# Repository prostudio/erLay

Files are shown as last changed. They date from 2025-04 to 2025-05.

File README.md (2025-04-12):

erLay is a ultra-portable CoreXY 3D printer made by [Evan Yu](https://evanyu.dev) and [Aaron Huang](https://runthebot.me)

This printer is built to print small parts needed fast at robotics competitions where our main limitations are space and time. This printer will mainly print spacers, shaft collars, pullies, etc.

## [BOM](https://docs.google.com/spreadsheets/d/1s7m9KlAu-EawWQ5k7trbtZSsV5alHb0_lQaYVRcTUCk/view) | [CAD](https://cad.onshape.com/documents/c8077fee67b983eb99774ac1/w/a53d436f84abc79ea5797123/e/d46022eb7d51b7e61800c962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) | [Journal](https://github.com/Badbird5907/erLay/blob/master/journal.md)

# Goals (we didn't manage to hit all of these within budget)
- Ultra-portable (for robotics competitions!!)
- Pico MMU (Optional) (Not in budget 😭)
- Zero Click ABL (Optional)
- Built-in carrying case (The printer will collapse into something like a pelican case) (Gave up on this one. see journal)
- Can be powered by a (multiple) power banks (Gave up on this one)
- NO STANDARD EXTRUSION (I think they look ewww and too normal)

# Features (Items in the final build)
- Locally sourced frame (Proudly Canadian)
- Easy to disassemble (8 Bolts)
- Core XY
- Klipper
- NeoPixel LEDs

3D Model

# Interesting note on design!
As you will notice, most of the frame is built out of linear rods. I was inspired by hex shafts in FRC and how we tap them and use a bolt to clamp both sides. I decided to do this for infill to maximize rigidity and minimize construction/deconstruction time.

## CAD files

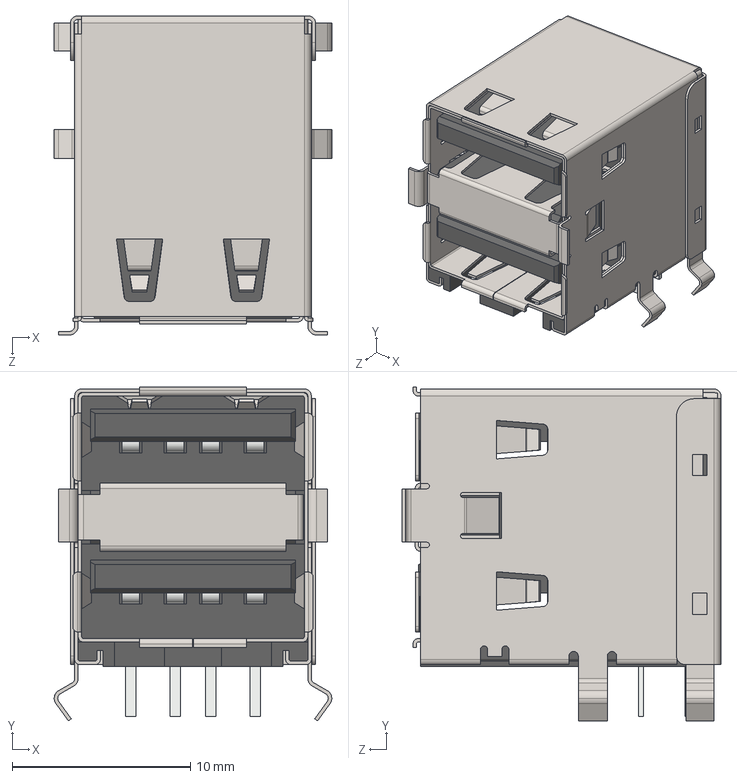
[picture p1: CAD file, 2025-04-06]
IOBoard/Components/usb double.step
15.6 x 18.7 x 17.9 mm

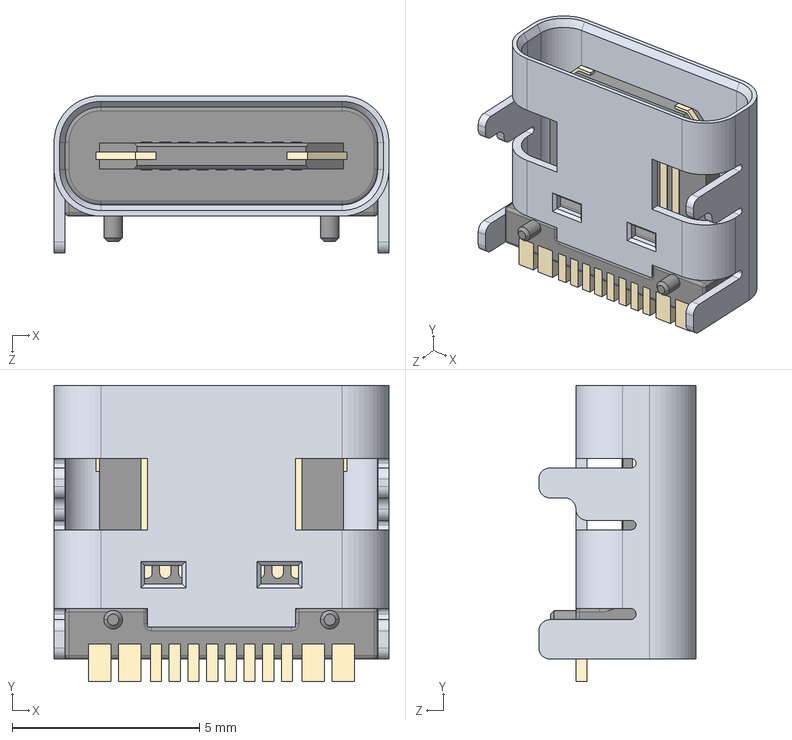
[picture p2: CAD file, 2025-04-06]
IOBoard/Components/usbc.step
8.94 x 7.90 x 4.20 mm

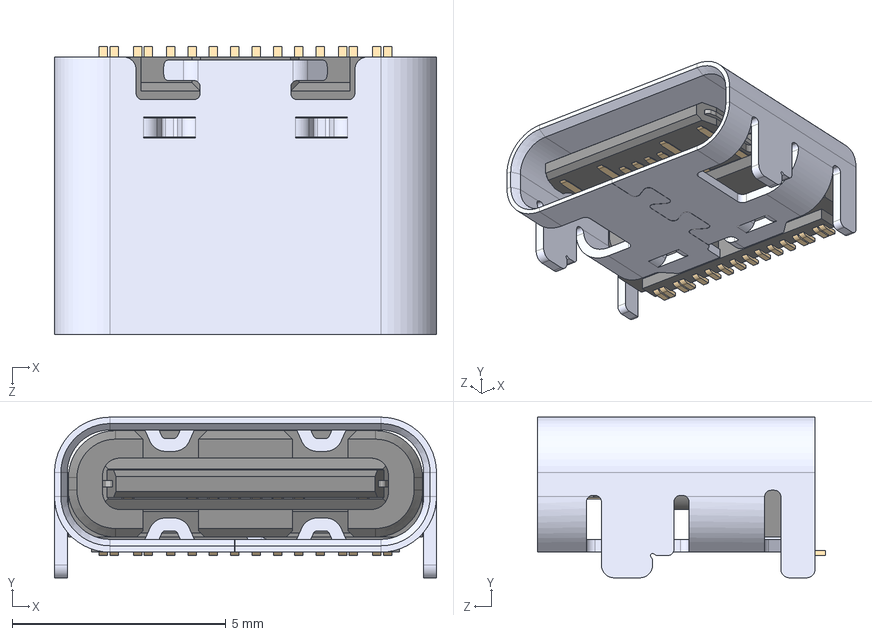
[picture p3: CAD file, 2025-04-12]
IOBoard/Components/2171790001.step
8.94 x 3.76 x 6.75 mm

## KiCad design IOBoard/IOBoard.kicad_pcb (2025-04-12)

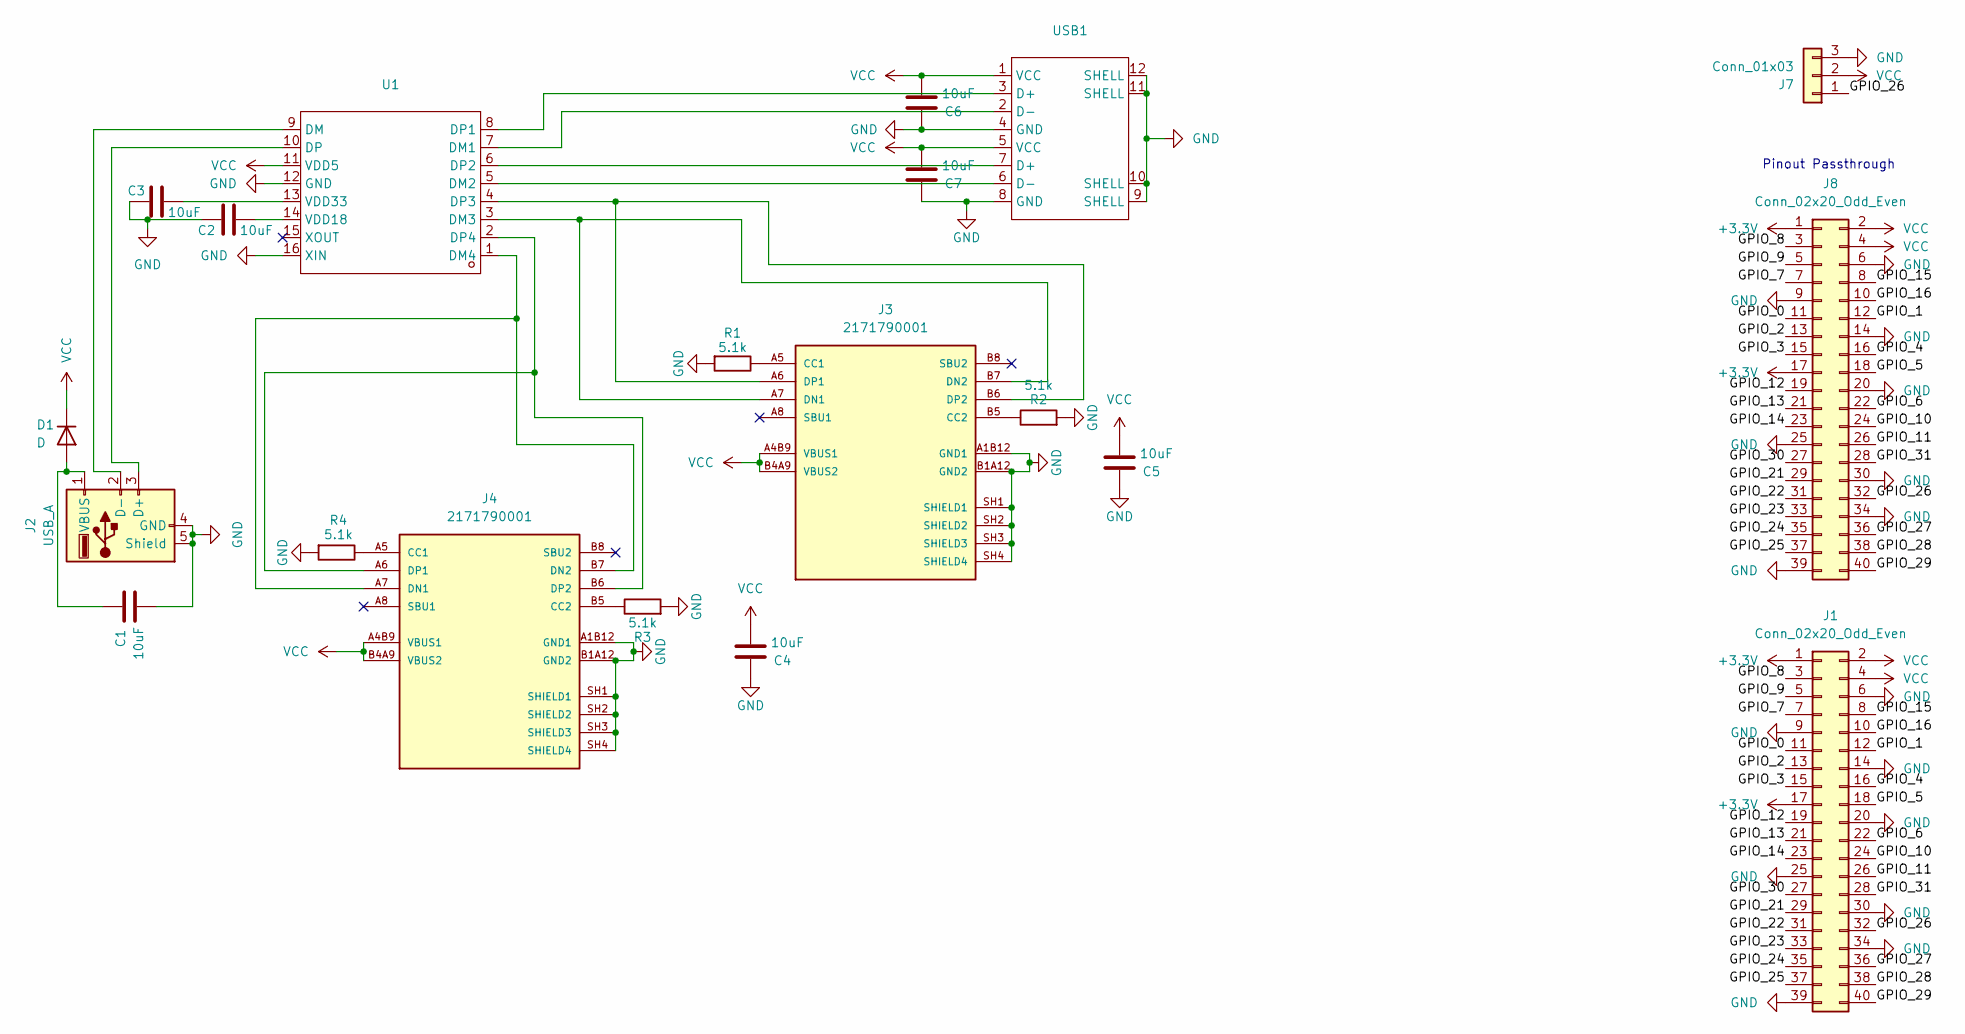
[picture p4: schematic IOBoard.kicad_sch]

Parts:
C1, C2, C3, C4, C5, C6, C7: 10uF; C_0603_1608Metric
D1: D; D_SOD-323
J1, J8: Conn_02x20_Odd_Even; PinHeader_2x20_P2.54mm_Vertical
J2: USB_A; USB-A-TH_USB-231-ARY
J3, J4: 2171790001; MOLEX_2171790001; PARTREV A1
J7: Conn_01x03; PinHeader_1x03_P2.54mm_Vertical
R1, R2, R3, R4: 5.1k; R_0603_1608Metric
U1: SL2.1A; Manufacturer Part SL2.1A; LCSC Part Name USB2.0高速4端口HUB控制器
USB1: USB-A-TH_AF-SS-JB17.6; Manufacturer Part AF SS-JB17.6; LCSC Part Name Type-A 母 弯插

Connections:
+3.3V: J1.1, J1.17, J8.1, J8.17
/GPIO_0: J1.11, J8.11
/GPIO_1: J1.12, J8.12
/GPIO_2: J1.13, J8.13
/GPIO_3: J1.15, J8.15
/GPIO_4: J1.16, J8.16
/GPIO_5: J1.18, J8.18
/GPIO_6: J1.22, J8.22
/GPIO_7: J1.7, J8.7
/GPIO_8: J1.3, J8.3
/GPIO_9: J1.5, J8.5
/GPIO_10: J1.24, J8.24
/GPIO_11: J1.26, J8.26
/GPIO_12: J1.19, J8.19
/GPIO_13: J1.21, J8.21
/GPIO_14: J1.23, J8.23
/GPIO_15: J1.8, J8.8
/GPIO_16: J1.10, J8.10
/GPIO_21: J1.29, J8.29
/GPIO_22: J1.31, J8.31
/GPIO_23: J1.33, J8.33
/GPIO_24: J1.35, J8.35
/GPIO_25: J1.37, J8.37
/GPIO_26: J1.32, J7.1, J8.32
/GPIO_27: J1.36, J8.36
/GPIO_28: J1.38, J8.38
/GPIO_29: J1.40, J8.40
/GPIO_30: J1.27, J8.27
/GPIO_31: J1.28, J8.28
GND: C1.2, C2.1, C3.1, C4.1, C5.1, C6.1, C7.1, J1.6, J1.9, J1.14, J1.20, J1.25, J1.30, J1.34, J1.39, J2.4 (GND), J2.5 (Shield), J3.A1B12 (GND1), J3.B1A12 (GND2), J3.SH1 (SHIELD1), J3.SH2 (SHIELD2), J3.SH3 (SHIELD3), J3.SH4 (SHIELD4), J4.A1B12 (GND1), J4.B1A12 (GND2), J4.SH1 (SHIELD1), J4.SH2 (SHIELD2), J4.SH3 (SHIELD3), J4.SH4 (SHIELD4), J7.3, J8.6, J8.9, J8.14, J8.20, J8.25, J8.30, J8.34, J8.39, R1.2, R2.2, R3.2, R4.2, U1.12 (GND), U1.16 (XIN), USB1.4 (GND), USB1.8 (GND), USB1.9 (SHELL), USB1.10 (SHELL), USB1.11 (SHELL), USB1.12 (SHELL)
unnamed: C1.1, D1.2 (A), J2.1 (VBUS)
unnamed: J2.3 (D+), U1.10 (DP)
unnamed: J2.2 (D-), U1.9 (DM)
unnamed: J3.A5 (CC1), R1.1
unnamed: J3.B5 (CC2), R2.1
unnamed: J3.A7 (DN1), J3.B7 (DN2), U1.3 (DM3)
unnamed: J3.A6 (DP1), J3.B6 (DP2), U1.4 (DP3)
unnamed: J4.A5 (CC1), R4.1
unnamed: J4.B5 (CC2), R3.1
unnamed: J4.A7 (DN1), J4.B7 (DN2), U1.1 (DM4)
unnamed: J4.A6 (DP1), J4.B6 (DP2), U1.2 (DP4)
unnamed: U1.7 (DM1), USB1.2 (D-)
unnamed: U1.5 (DM2), USB1.6 (D-)
unnamed: U1.8 (DP1), USB1.3 (D+)
unnamed: U1.6 (DP2), USB1.7 (D+)
unnamed: C2.2, U1.14 (VDD18)
unnamed: C3.2, U1.13 (VDD33)
VCC: C4.2, C5.2, C6.2, C7.2, D1.1 (K), J1.2, J1.4, J3.A4B9 (VBUS1), J3.B4A9 (VBUS2), J4.A4B9 (VBUS1), J4.B4A9 (VBUS2), J7.2, J8.2, J8.4, U1.11 (VDD5), USB1.1 (VCC), USB1.5 (VCC)

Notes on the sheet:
Pinout Passthrough

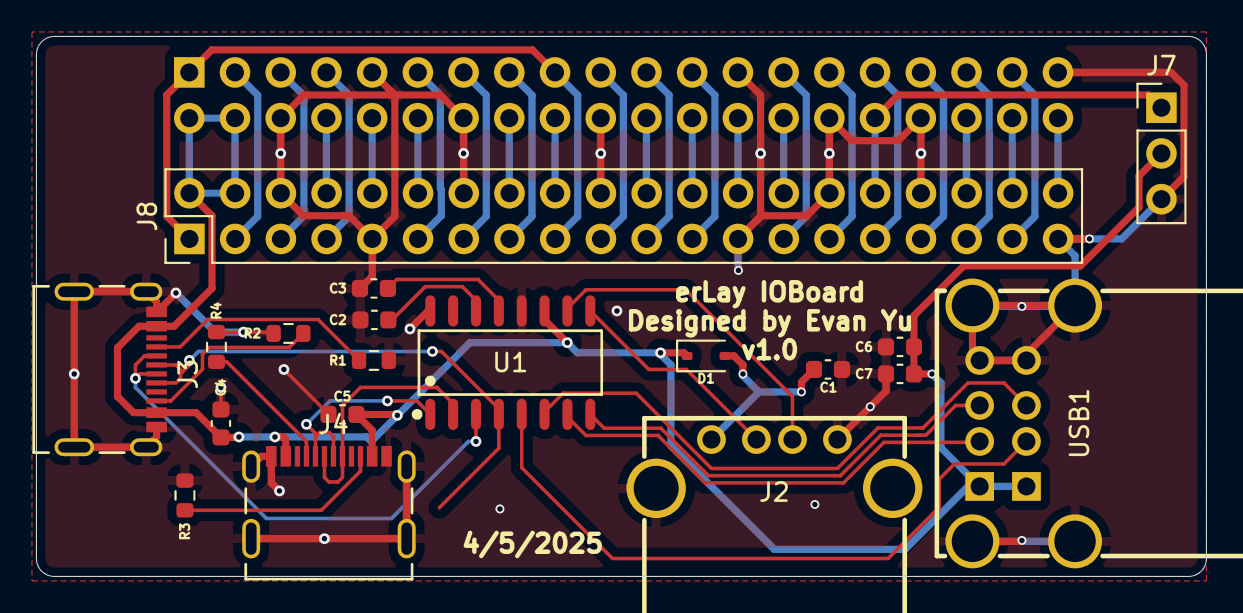
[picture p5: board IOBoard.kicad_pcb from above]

Board: 2 copper layers, 65.0 x 30.0 mm, 20 parts (1 on the bottom side), 48 nets.

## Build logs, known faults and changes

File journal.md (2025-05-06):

erLay is a ultra-portable CoreXY 3D printer made by [Evan Yu](https://evanyu.dev) and [Aaron Huang](https://runthebot.me)

This printer is built to print small parts needed fast at robotics competitions where our main limitations are space and time. This printer will mainly print spacers, shaft collars, pullies, etc.

## [BOM](https://docs.google.com/spreadsheets/d/1s7m9KlAu-EawWQ5k7trbtZSsV5alHb0_lQaYVRcTUCk/view) | [CAD](https://cad.onshape.com/documents/c8077fee67b983eb99774ac1/w/a53d436f84abc79ea5797123/e/d46022eb7d51b7e61800c962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) | [Journal](https://github.com/Badbird5907/erLay/blob/master/journal.md)

# Goals
- Ultra-portable (for robotics competitions!!)
- CoreXY
- Pico MMU (Optional)
- Zero Click ABL
- Built-in carrying case (The printer will collapse into something like a pelican case)
- Can be powered by a (multiple) power banks

# Total Time

Aaron: 103.5h
Evan: 77.5h

# Feb 12 2025

- Came up with name, specs, and design.
- Research on different 3d printer designs & parts (VORONDesign, etc...)
- Started options for BOM

Evan: 2h
Aaron: 4h

## Both
### What was done:
- Discussed name, specs and design
- Rabbit holing and yapping about option
- Both already have 3D printers
### Some of our other ideas:
- 2/3 stage elevator on a bed slinger 💀
- smaller Voron v0

## Aaron

- I'm the one that dragged other bozo onto this
- I am in the process of building a [Hex Zero](https://github.com/Alexander-T-Moss/Hex-Zero)
- Went down a printer rabbit hole

### ABL:
- [ZeroClick](https://github.com/zruncho3d/ZeroClick)
- Seams nice and cheap
- Used on Hex Zero
- ABL needs more research

### Hotend/Toolhead:

Requirements:
- COTS
  - We do not want to be designing a Toolhead
  - We can use a custom one if it relly came to it
- Direct drive
  - Keep it compact
  - Print filaments that are harder to print (Remember robotics!)

Options:
- [Apogee Extruder](https://www.filastruder.com/products/ldo-apogee-toolhead-for-ender-3)
  - Light 170g
  - Cheap
- [Creality Sprite](https://www.creality.com/products/sprite-extruder-pro-kit)
  - Kinda heavy 266g
  - Dual-Gear Drive for flexibles
  - Cheap
- [BIQU H2](https://biqu.equipment/products/biqu-h2-v2s-extruder-for-b1-bx-ender-3-3-v2-5-6-cr6-10?variant=40218342555746)
  - Dual-Gear Drive for flexibles
  - Weight ok 195g
  - Cheap ish
  - Big
- [**Orbiter**](https://www.3dlabtech.ca/product/ldo-smart-orbiter-extruder-kit-v3/)
  - Probably this?
  - Cheapish
  - Canadian website???
  - We are Canadian so no tarifs!!?!??!?
  - Light 175g
  - Dual-Gear Drive for flexibles
  - With a CHT nozzle??!!!?!?
  - WHAT??? for 87 USD?????? (The Canadian dollar is not doing so well)

Ok that's it for today I have school tmr

# Feb 13 2025

Aaron: 5h
Evan: 2h

## Aaron:

Yay snow day!!! 
Ok so I was losing my mind at midnight yesterday and did not realize that the Apogee uses an orbiter
I probably need to find a better source

### Frame

I was brainstorming frames today and I wanted the hingeing lid of the case to be the Z-axis
I started with some CAD (Bad idea) and I got almost nowhere

Anyway I do here are the current frame options after spending 30 mins failing at CAD:
- Hingeing lid with the bed in the middle
- Linear Rods as the Z-axis support (Similar to Neutrino)

I also started a basic Onshape Part Lib and did a lot more research

I've learnt my lesson and now will spend the next hour **drawing concepts** before CADing

### Drawings

I spend half an hour making a Iso Grid YAY!
Anyway Heres the idea
3D Printer Concept Iscometric

## Evan:

Spent most of the day working on [makropad](https://github.com/Badbird5907/makropad), it's almost done!

### Research:
- Researched how CoreXY works
  - https://corexy.com/theory.html
  - https://all3dp.com/2/corexy-3d-printer-is-it-worth-buying/
  - https://3ddistributed.com/belt-frequency-and-tensioning/
  - 3 Stepper Motors:
    - 2 for the XY
    - 1 for the Z
  - Print head is fixed to XY axis, while z axis is moved for printing
  - Belt frequency can differ between machines
  - Tensioning is important for performance. Frequency can affect speed and print quality
  - Over-tensioning can cause the belt to slip/wear out faster
  - Tighten belt until there is some resistance when pushed. There should be no slack.
  - Looser belt = layer shifting when printing (misaligned prints)
  - Failure can be caused by:
    - Belt friction
    - Damaged belt teeth
    - Slip/rubbing of the belt
    - Debris
  - Loose/missing pulley teeth can cause jerky movements
  - Pitch = distance between teeth (most are 2mm)
Pros of CoreXY:
- Speed
- Accurate
- Compact
- Rigid frame
This makes it perfect for our use case, as we want a small and fast printer we can take to competitions (hackathons and FRC).

Limitations:
- Complex assembly
  - This could be an issue for portability, if we need to disassemble the printer.
- Higher cost
- Z axis constraints

Reference Mechanism

[CoreXY vs Bedslinger](https://store.creality.com/blog/corexy-vs-bed-slinger)

Bedslinger:
- Advantages:
  - Simple assembly
  - Affordable
  - Easy to use
- Disadvantages:
  - **Inertia** caused by the bed moving
  - Speed is slower due to bed inertia 
  - Higher vibration due to bed movement
  - As size of bed increases, the slower the printer has to be due to higher weight

## Aaron Part 2:
I've been laying out the printer

So the idea was to have both the gantry and the bed fold up but after an hour of layout it looks pretty impossible with the stock Voron 0 layout
Voron Layout

There's also a concept sketch that I will put on here sometime

### Feb 14 & 15 2025

Evan: 0h
Aaron: 0h

random thought from Evan: What if the Z axis was telescoping or something


14th: We spent the day preparing for a robotics competition

15th: Competition Day

# Feb 17 2025

Evan: 2h
Aaron: 0h

## Evan
Researched other people's custom CoreXY builds:
1. https://www.instructables.com/CoreBot-CoreXY-3D-Printer/ **this is a really good blog/guide**
 - X/Y Movements: 12mm y / 9mm x linear rails
 - Z: 2x 10mm lead screws + 4x 12mm smooth rods.
 - At the length of spindels, constraint the spindle at top + bottom to keep distortion/ghosting low
 - Long travel distances will cause bowden tube to flex, causing friction + jams
 - Frame assembly should be straight forward
2. https://www.instructables.com/How-to-Design-and-Build-a-3D-Printer/
 - 3030 extrusions have higher rigidity
 - Aluminum is cheap, light, and can be anodized
 - Aluminum extrusions can be connected in many ways
 - Blind joints = lower part count, less tollerences to worry abt, simple
 - CoreXY reduces weight by putting motors on frame rather than head
 - Can accel head much harder with less inertia
 - Instead of X/Y motors, there are A/B motors, connected directly to the XY belts
 - Belt loop allows for a gear ration between motor and CoreXY belt. (see the writeup for full info)
 - GT2 belts are cheap and easy to source
 - Belts can be run along the inside of frame
 - Bed is 8mm thick aluminum tooling plate
 - Significant thermal mass = stable temps
 - Thick = less bed warping
 - 200w DC silicone heater under bed
 - Can be replaced with PCB heated bed
 - Extruder w/ 3:1 gear ratio = finer control of filament
 - Hot end is where plastic is heated and extruded

# Feb 22 2025

Evan: 2h
Aaron: 10h

## Aaron
### Folding Printer (Frame V1, V2, V3)
V1 and V2
This is how 2 different versions of the frame would fold. I layed out V1 a while back and it did not fit. 
V2 also has problems with the center of gravity.
V3
This is the latest frame that we have made. It will have a bed on one side and a gantry on the other. This frame costs way too much and it still needs a gantry and a bed

### New idea
Instead of making it fold and making it fast, go all out on the portable aspect and make the printer powered off a USB c power bank (100W)

## Evan
### Researched different power supplies
- Our power budget should be around <=180W
- USB-C PD
 - Can supply up to 240W
 - Maybe we can pull either 180-240w from a single USB-C PD supply
 - High wattage is _expensive_ (easily $50-100+)
 - Or we can pull 60w from 4 power banks, allowing hot swapping power supplies on the fly. Also much cheaper since lower wattage per power bank
 - Concern: how long the power banks will last
 - I'm probably going to design a custom PCB to do this
  - Suitable(?) controllers:
   - [TPS25750](https://www.ti.com/product/TPS25750)
   - [STUSB4500](https://www.st.com/en/interfaces-and-transceivers/stusb4500.html)
 - I want to keep the cost of the PCB as low as possible, the STUSB4500 is probably the best as it has way more stock on LCSC (8.3k vs 14) than the TPS25750, and is 20c cheaper.
- Use a LTC4370 to load share between the different supplies
- Use Diode OR-ing or Ideal Diode controllers to isolate power supplies and prevent **backfeeding**
- Also made our hours auto update via github actions + a python script
- 
## Aaron 
Spent a lot of time researching Linear rails/rods and how to hold a heated bed.
A lot of Cadding

# Feb 24 2025

Evan: 2h
Aaron: 1h

Discussed details over dinner.
### USB PD Power Supply
- 240W power budget (400 max but we wont be testing this)
- Load balancing (diodes) / backfeeding
- Boost -> 24v
- Screw terminal output
- Automatic negotiation
- 4 USB-C inputs
- Screw terminal input (bypasses load balancer and connects directly to output screw terminals)
 -> (For testing)
- Boost every input before load balancing to prevent issues w/ voltage diff
- Pico negotiates even wattage from all to reduce load on balancer
- Digitally set target voltage via pico (?)

# Feb 25 2025

Evan: 1h
Aaron: 0h

Did some research on USB-C PD controllers.
There are a couple options, but i've only looked at two so far:

| Name | Max V | Max A | Max W | I2C Address Configurable | Notes | Suitable |
|---|---|---|---|---|---|---|
| [TPS65987D](https://www.ti.com/lit/ds/symlink/tps65987d.pdf) | 20V | 5A | 100W  | Yes (ADCIN1/ADCIN2) | Address configured with Analog signal(?) | Yes |
| [STUSB4500](https://www.st.com/resource/en/datasheet/stusb4500.pdf) | 20V | 5A | 100W  | Yes (ADDR0/ADDR1) | MAX 4 on 1 i2c line. (See 4.1) | Yes |
| [FUSB302](https://www.onsemi.com/download/data-sheet/pdf/fusb302b-d.pdf) | 20V | 5A | 100W  | No | | No |

# Feb 24-26
Aaron: 3h
Evan: 3h

## Aaron
Decided to build a custom tool head similar to ESO3D. CADing that and gantry.

Inspiration:
ESO3D
Creality K1
Voron V0

## Evan
Did some research on the RP2350. Read through the [integration guide](https://datasheets.raspberrypi.com/rp2350/hardware-design-with-rp2350.pdf) and [datasheet](https://datasheets.raspberrypi.com/rp2350/rp2350-datasheet.pdf).
We'll probably use the A variant over the B variant as we only need the I2C.

# March 9-11
Aaron: 36h
Cadding









# March 23
Evan: 2h

## Evan
Did some research into the USB PD 3.0 spec (specifically PPS). Currently, there doesn't seem to be a (cheap) sink ic that supports PPS and a **configurable** i2c address.
I basically want the [AP33772S](https://www.diodes.com/datasheet/download/AP33772S.pdf) but with a address configuration function (it has a static address of 0x52)

Also watched [Phil's Lab #104](https://www.youtube.com/watch?v=W13HNsoHj7A) and [#114](https://www.youtube.com/watch?v=kUruN6WBgSw)

# March 24
Aaron: 2.5h



Made a master sketch for the bed and the actual bed mount.
Made of 0.75in square extrustion

# March 26
Evan: 6.5h

## Evan
I spent most of my time trying to figure out how to design the schematic. A major blocker I'm stuck at right now is *how* to power the rp2040. Because I want the power banks to be hot-swappable, I need to power the rp2040 off any one of the USB-C ports, and I don't want to add a buck converter for each port... Things can get expensive *quickly*.

*This is likely a fire hazard :trollface:*

Current progress:



The PSU is being developed in [Badbird5907/PDSU](http://github.com/badbird5907/PDSU)

I'm probably going to just buck the voltage for each USB port with 4x TPS54331 and use diode OR-ing if I don't have any better ideas tmr morning.

# March 29
Aaron: 3h

Added Z-Axis Motor. Way too painful


# March 30
Evan: 6h

Did a bunch of research/video watching, and some chatgpt-ing.
The MCU will likely pull its voltage from a step-down converter after the diode ORing to keep costs down. I still have my doubts weather this will work or not...

# March 31
Evan: 3.5h

The PD controllers are complete, now I need to figure out how to load balance and combine the inputs. Right now i'm trying to find the perfect buck/boost VRM that's cheap enough to get 4 of.

# April 1 & 2
Evan: 4h

STILL trying to find a suitable buck/boost VRM. I found the XL6019, which is PERFECT... *except* it's max switching current is 5A, which is does not work well for our design, which pushes 20A/3A -> 12V/5A (60W) through. That means our **switching current** (the current that flows through as it makes/breaks contact) is about 8.53A, which is way too high for this chip and will likely burn it.
I found the LT8645S, which seems to support our use case and switching current, however it costs $8.77 each, making it prohibitively expensive as we need 4 per board.

[4pm] I'm going to spend the next few hours looking through MORE datasheets... I'm going to see if it costs less to use a MOSFET **controller**, which should be cheaper and allow for more current as these controllers do not include a FET. 

# April 3
Evan: 0.5h

I've decided to temporarily pause development on the power supply PCB, as I don't think it's very feasible to complete in the next few days (infill is due April 7), so I will be spending
the next few days developing and prototyping a esp32 daughter board with a touchscreen LCD.

**Even if I was able to complete the PCB on time, It has a pretty high chance of going up in flames, potentially damaging the power banks, or destroying the components. I really do want a printer that can be powered off a power bank, but it really isn't feasable to make __safely__ in the time I have right now. I will very likely continue development on this PCB after infill**

Right now, I think i'm going to use an ILI9341 TFT touchscreen that is driven over SPI with an ESP32 as these displays are generally [pretty cheap](https://www.aliexpress.us/item/2251832829271342.html)

# April 4
**CHICKEN JOCKEY**

**FLINT AND STEEL**

Evan: 2h

## Evan
Watched the minecraft movie with Aaron (11/10 btw). We discussed options for the PCB design for erLay afterwards.
The consensus we landed on was that I would develop a HAT for the raspberry pi zero w that would be running klipper, as
Aaron already had a touchscreen for the pi. (that would just use klipperscreen)

This HAT would break out and expose LED pins/controllers. It will also act as a USB hub reducing the need for janky micro-usb connectors.

[1:26 AM - Apr 5] - The USB hub schematic is completed. It uses an SL2.1A USB hub controller, which is a pretty standard USB hub controller. It has 4 downstream ports (2x A, 2x C), and 1 upstream port (USB A).

# April 5
Evan: 7.5h

## Evan
I spent most of the day (1pm-9pm) updating the HAT schematic, placing the parts, routing the pcb, and sourcing the parts.

3D View
kicad_AbbpzV4n1V

PCB


Also my hackpad stuff arrived! (check my personal channel on slack, #evans-basement)

# April 6
Evan: 3h

Sourced parts and made the [BOM](https://docs.google.com/spreadsheets/d/1s7m9KlAu-EawWQ5k7trbtZSsV5alHb0_lQaYVRcTUCk/view) - Our total comes out to $300.83 USD, 83 cents over budget!!!

<rant>
**TW: Incoherent rambling**
I really wanted our printer's *gimmick* to be powered off all USB-C power banks, and I spent a considerable amount of time towards developing this.
  
If it wasn't for midterms, I would have had enough time to sink into getting this thing properly spec'd out and designed *within budget*. I know that printers for infill should have something that sets them apart, but without this pcb, we're just yet another generic klipper CoreXY.
  
There were a couple reasons why didn't happen:
- Midterms/no free time
- My little experience in real electrical design
- Insisting on a variable voltage output- not just 12 or 24v
- The ambitious scope I set out for this
- Not being able to find a VRM that was cheap enough to use in our design that:
  a) can handle around 60W each (this is the very upper limit of *integrated FET* buck/boosts)
  b) have minimal supporting circutry as I would need to manually place and route four of these buck/boost converters

If I hadn't insisted on a variable voltage, and if I was didn't care about placing (a lot) more components, there would be a better chance that this project would have turned out the way I wanted it to. It would be even more likely to be completed if I was willing to reduce the scope, instead of boneheadedly smashing my head on my keyboard trying to figure out how to make this work.
  
Even if I did get this thing designed in time, it would more than likely fail...
Best case scenario: nothing happens, worst case scenario: I burn down my house
realistically speaking, it would could damage a lot of pricey usb c PD chargers, the printer itself, the (somewhat expensive) components on the pcb, or all... Especially since this is about 200 watts of power i'm playing with.

don't know where i'm going with this incoherent rambling mess but yeah :(
</rant>

## April 11
Evan: 5h

# Evan
Just spent a good chunk of time redoing/resourcing a good chunk of the BOM, sourcing parts off digikey instead of LCSC, and reworking parts of the PCB to make it work with parts from Digikey. We're also adding Auto Bed Leveling!
Our total comes out to approx. $283 USD!





# April 12
Evan: 2h

# Evan
Finally got the grant! I purchased the extruder and hotend off of trianglelab.net instead of aliexpress as they are on sale today. I've also ordered everything else off Aliexpress, Digikey, and JLC.

# Apr 22/23
Evan: 4h
Parts arrived, I spent a LONG TIME trying to solder the tiny 0402 components D:

# Apr 21-27

Aaron: 7h

I went and bought 3/4"x3/4" box tube from home depot

Designing and prototyping templates for manufacturing (I'm so sad I don't have access to a CNC)


Lots of highly accurate parts made!


# Apr 28-30
Aaron: 8h

Bought 7.5ft of linear rod. Attemped to drill. Gave up. Even just cutting takes way too long.

## Somewhere in this time frame
Aaron: 4h
Evan: 4h
Trip planning. SOOOOOOO many routes :(

# May 1-2
Aaron: 4h
Evan: 5h

## Aaron
Some assembly, lots of 3D printing, more manufacturing.

## Evan
Setting up the pis, klipper, and assembling the electronics.
*MLH gave me a defective pi zero :(*

# May 3-4
Aaron: 12h
Evan: 4h
## Aaron
A lot of assembly, 3d printing. Again, Stainless is a pain to work with, do not recommend. 

Way too much filing. Spent too long looking for a lost linear bearing (Found it yay!)

## Evan
Spent some time destroying another pi zero, then configuring klipper and our current pi 4b. It now starts an AP called `erLay` on boot, so we don't need to have an ethernet cable plugged in all the time.

# May 5
Evan: 4.5h
Aaron: 4h

## Evan
Went to Aaron's house and brought all the electronics, assembled most of the toolhead, base, and cut out some polycarbonate.
Brought the toolhead home to solder on longer wires for the fans (not proud of the soldering job but I think it works.)

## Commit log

2025-04-05 Initialize IOBoard kicad project
    [IOBoard.kicad_pcb, IOBoard.kicad_sch]
2025-04-05 complete schematic for usb hub
    [IOBoard.kicad_sch]
2025-04-06 feat: complete IOBoard
    [IOBoard.kicad_pcb, IOBoard.kicad_sch, freerouting.dsn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]
2025-04-07 optimize pcb (yesterday)
    [IOBoard.kicad_pcb, freerouting.dsn, temp-freerouting.dsn]
2025-04-12 Update IOBoard usb c connectors
    [2171790001.step, IOBoard.kicad_pcb, IOBoard.kicad_sch]
